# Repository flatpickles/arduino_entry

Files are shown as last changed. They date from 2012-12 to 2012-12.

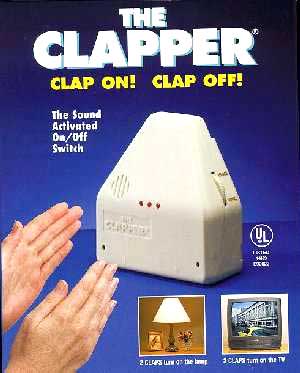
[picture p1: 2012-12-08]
final_paper/the-clapper.jpg

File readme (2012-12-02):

Arduino Entry System
Fall 2012
Andy Chen, Max Lesser, Matt Nichols

OVERVIEW

This project is a reasonably straightforward Arduino program which enables pulling the deadbolt from the inside of a door once a specific pattern of knocks has been detected. This pattern is configurable via a "record" function, and, when powered, the device is always listening for the pattern, ready to trigger a motor to pull the deadlock.

DESIGN

This program assumes a hardware configuration that includes a piezo element for knock sensing (connected on "piezo_pin", in our code), two LEDs for control output, a button to trigger the recording mode, and a servo ("s1", connected on "servo_pin") to pull the deadbolt.

The device begins with a default knock pattern of ten equally spaced knocks. In our system, a n knock pattern is represented as a n-1 sized array, each element being the ratio between adjacent knocks (so the default knock pattern is represented as [1, 1, 1, 1, 1, 1, 1, 1, 1]). When the system hears a first knock, it will begin recording the time offsets between subsequent knocks, and after a timeout (i.e. the knock has completed) relative ratios are calculated from the recorded offsets. Each of these ratios are then compared to those of the current key pattern (within an error margin), and if they all match then the servo is triggered and the deadbolt is pulled open.

Recording is very similar: pressing the button triggers record mode, and then the current key pattern will be replaced by whatever ratioed pattern is recorded after the button press (and before a timeout, as above). This pattern will then be played back to the user on a LED, and the device will re-enter normal operation, listening for entry attempts.

USE

Installation: the device must be installed such that the piezo is pressed directly against the door, to best register knocking. The servo should be configured to pull the deadbolt out when it rotates (the user will need to handle re-locking the door).

Recording: press the button once, and then knock out the desired pattern on the inside of the door. Wait for the timeout, and then make sure the replayed pattern (on the second, lower LED) is as you desire. Your patterns must consist of between three and ten knocks (inclusive); shorter knocks will not overwrite the current key pattern, and recording will cut off after ten knocks.

Unlocking: simply knock the pre-recorded pattern on the outside of the door, and if the time ratios between your knocks match the stored key pattern, the servo will pull the deadlock. It must be manually re-locked afterwards. If you make a mistake in the pattern, wait four seconds (the timeout) and try again.

NEXT STEPS

In the remote_unlock/ directory of the repo, we have the backend/server script for implementing SMS-triggered unlocking as well (via Twilio). Alas, we haven't yet had any successes in configuring the device's side of this functionality; however, should the device be configured with an ethernet shield, it would be simple to poll against [server port]/state and trigger the servo when the "Unlocked" state is observed.

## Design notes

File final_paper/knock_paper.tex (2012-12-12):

%==============================================================================
% Matt Nichols' Homework Template
%==============================================================================

%Fill out this line with the homework number
\newcommand{\visibleusernames}
{\space man1, malesser, ac110 }
{}
\newcommand{\thisclass}{CSCI 160}
\newcommand{\thishw}{Final Project}

%==============================================================================
% Formatting parameters
%==============================================================================

\documentclass[11pt]{article}			% 11pt article
\author{Matt Nichols}
\date{\today}
\makeatletter					% Make '@' accessible.

%Fill out this line with your name and login
\def\@oddhead{\bf \thisclass \space - \thishw\hfill \visibleusernames} % Here they are

\oddsidemargin=0in				% Left margin minus 1 inch.
\evensidemargin=0in				% Same for even-numbered pages.
\textwidth=6.5in				% Text width (8.5in - margins).
\topmargin=0in					% Top margin minus 1 inch.
\headsep=0.2in					% Distance from header to body.
\textheight=8.5in					% Body height (incl. footnotes)
\skip\footins=4ex				% Space above first footnote.
\hbadness=10000					% No "underfull hbox" messages.
\makeatother					% Make '@' special again.

%==============================================================================
% Packages used
%==============================================================================

\usepackage{amsmath}				% want AMS fonts
\usepackage{amssymb}
%\usepackage{psfig}				% want to include EPS files
\usepackage[pdftex]{graphicx}				% for including images
\usepackage{algorithmic}
\usepackage{algorithm}
\usepackage{hyperref}
\usepackage{tikz}

%==============================================================================
% Macros
%==============================================================================
\newcommand{\new}[1]{{\em #1\/}}		% New term (set in italics).
\newcommand{\set}[1]{\{#1\}}			% Set (as in \set{1,2,3})
\newcommand{\setof}[2]{\{\,{#1} $\mid$~{#2}\,\}}	% Set (as in \setof{x}{x > 0})
\newcommand{\N}{\mathord{\Bbb N}}		% Positive integers.
\newcommand{\compl}[1]{\overline{#1}}		% Complement of ...            
\newcommand{\bigand}{\bigwedge}
\newcommand{\bigor}{\bigvee}
\newcommand{\OR}{\vee}
\newcommand{\AND}{\wedge}
\newcommand{\code}[1]{\texttt{#1}}
\newcommand{\nlogn}{n \log n}

\newcounter{qcounter}
\setcounter{section}{0}
\def\thesection{Section \arabic{section}}

% \begin{list}{b\alph{qcounter}.}{\usecounter{qcounter}} <-- helpful

%==============================================================================
% Title
%==============================================================================

\begin{document}
\centerline{\bf \LARGE\thishw: Knock Detection Entry System}
\centerline{\today}

\section{Introduction}
 % Introduce your project. Succinctly explain your problem and solution. Why did you choose to work on it?
Carrying keys around has always been a hassle for all of us. If one loses a key, he or she has to be assisted by someone else to get in to the room. In addition, there are many situations where you wouldn't want to bring your keys with you either, such as when you're going on a run. We wanted an easier way to enter and exit a locked room, and not ever have to worry about being locked out. 

Our project involves an Arduino program which enables pulling a door handle down from the inside of a door once a specific pattern of knocks has been detected. This pattern is configurable via a ``record" function, and, when powered, the device is always listening for the pattern, ready to trigger a motor to open the door. If an incorrect knock pattern is given, the program alerts you through a buzz in the speaker. This way, the room is secure, and you'll never be locked out because you don't have the key.

\section{Architecture}
% Describe the architecture of your system. Figures are welcomed and encouraged

\subsection{Hardware Design}

This program assumes a hardware configuration that includes a piezo element for knock sensing (connected on \verb|piezo_pin|, in our code), two LEDs for control output, a button to trigger the recording mode, a servo (\verb|s1|, connected on \verb|servo_pin|) to pull the deadbolt, and a second piezo speaker to buzz when an incorrect pattern is recognized, or the system times out (and starts waiting for another knock series).

The wiring of the system ended up being pretty straightforward (see diagram below). The piezo on the left is for audio output (signaling error events or a reset of the listening system) and the piezo on the right (highlighted in purple) is used for knock detection. The left (red) LED blinks whenever a knock is detected (mainly a debugging tool for us, though also helpful when the user is recording), and the right (green) LED is a control signal: it is turned on during recording, and is used to both signal a timeout event (reset of input knock pattern) and to replay a knock pattern to the user after it has been recorded. When the system receives a correct knock pattern, it will rotate the servo 180 degrees (enough to pull down a door handle or draw back a deadlock), wait a few seconds, and then rotate back to its original position. The rest of our hardware implementation is reasonably simple, but is diagrammed in full below.

\begin{center}

\end{center}

\subsection{Software Design}

Left to describe is the operation of our software which is running on the Arduino, which is strictly procedural and adheres to a predetermined flow (i.e. we do not make use of interrupts on the Arduino platform).

The basic operation of our software can be summed up well as a finite state machine (below). The system's default state is iterating within the Arduino main loop, waiting for either a button press or a knock. At both \verb|Input| and \verb|Record|, it will continue listening for subsequent knocks, though the transitions out of these states are different: at \verb|Input|, it will only move on to evaluation of the knock pattern once \verb|n knocks| (the number of knocks in the current valid pattern) have been detected, while at \verb|Record|, it will wait for a timeout (i.e. knocking has stopped) or until the user has input the maximum allowable number of knocks to progress to the next state. Along both the \verb|timeout| and \verb|incorrect| edges, a sound will be played on the speaker. The \verb|Print| state corresponds to a blocking process during which the current valid pattern is echoed in appropriately spaced blinks on the control LED, and after this completes, it returns to its normal resting state. The rest of the system's operation within the state diagram should be self-explanatory, though we delve into a few more details (outside of the FSM) below.

\begin{center}
\begin{tikzpicture}[scale=0.2]
\tikzstyle{every node}+=[inner sep=0pt]
\draw [black] (26.6,-22.6) circle (3);
\draw (26.6,-22.6) node {$Loop$};
\draw [black] (55,-41.3) circle (3);
\draw (55,-41.3) node {$Input$};
\draw [black] (67.6,-23.2) circle (3);
\draw (67.6,-23.2) node {$Record$};
\draw [black] (26.6,-51.2) circle (3);
\draw (26.6,-51.2) node {$Check$};
\draw [black] (6,-51.2) circle (3);
\draw (6,-51.2) node {$Open$};
\draw [black] (6,-51.2) circle (2.4);
\draw [black] (26.6,-7.6) circle (3);
\draw (26.6,-7.6) node {$Print$};
\draw [black] (29.6,-22.64) -- (64.6,-23.16);
\fill [black] (64.6,-23.16) -- (63.81,-22.64) -- (63.79,-23.64);
\draw (47.08,-23.48) node [below] {$button\mbox{ }press$};
\draw [black] (29.11,-24.25) -- (52.49,-39.65);
\fill [black] (52.49,-39.65) -- (52.1,-38.79) -- (51.55,-39.63);
\draw (37.85,-32.45) node [below] {$knock$};
\draw [black] (23.713,-23.373) arc (312.7283:24.7283:2.25);
\draw (19.24,-20.97) node [left] {$no\mbox{ }input$};
\fill [black] (24.23,-20.78) -- (24.05,-19.85) -- (23.32,-20.53);
\draw [black] (52.49,-39.65) -- (29.11,-24.25);
\fill [black] (29.11,-24.25) -- (29.5,-25.11) -- (30.05,-24.27);
\draw (44.45,-31.45) node [above] {$timeout$};
\draw [black] (52.17,-42.29) -- (29.43,-50.21);
\fill [black] (29.43,-50.21) -- (30.35,-50.42) -- (30.02,-49.48);
\draw (37.07,-45.62) node [above] {$n\mbox{ }knocks$};
\draw [black] (23.6,-51.2) -- (9,-51.2);
\fill [black] (9,-51.2) -- (9.8,-51.7) -- (9.8,-50.7);
\draw (16.3,-50.7) node [above] {$correct$};
\draw [black] (57.982,-41.109) arc (121.40093:-166.59907:2.25);
\draw (61.97,-44.82) node [right] {$knock$};
\fill [black] (56.97,-43.55) -- (56.96,-44.49) -- (57.81,-43.97);
\draw [black] (26.6,-48.2) -- (26.6,-25.6);
\fill [black] (26.6,-25.6) -- (26.1,-26.4) -- (27.1,-26.4);
\draw (27.1,-36.9) node [right] {$incorrect$};
\draw [black] (7.75,-48.77) -- (24.85,-25.03);
\fill [black] (24.85,-25.03) -- (23.97,-25.39) -- (24.78,-25.98);
\draw (16.89,-38.28) node [right] {$timeout$};
\draw [black] (64.8,-22.13) -- (29.4,-8.67);
\fill [black] (29.4,-8.67) -- (29.97,-9.42) -- (30.33,-8.48);
\draw (55.86,-14.69) node [above] {$timeout\mbox{ }/\mbox{ }max\mbox{ }knocks$};
\draw [black] (26.6,-10.6) -- (26.6,-19.6);
\fill [black] (26.6,-19.6) -- (27.1,-18.8) -- (26.1,-18.8);
\draw (26.1,-15.1) node [left] {$done\mbox{ }printing$};
\draw [black] (69.27,-20.722) arc (173.74488:-114.25512:2.25);
\draw (74.12,-18.63) node [right] {$knock$};
\fill [black] (70.58,-23.02) -- (71.32,-23.6) -- (71.43,-22.61);
\draw [black] (56.71,-38.84) -- (65.89,-25.66);
\fill [black] (65.89,-25.66) -- (65.02,-26.03) -- (65.84,-26.6);
\draw (61.9,-33.61) node [right] {$button\mbox{ }press$};
\end{tikzpicture}
\end{center}

The device begins with a default knock pattern of ten equally spaced knocks. In our system, an $n$ knock pattern is represented as a $n-1$ sized array, each element being the ratio between adjacent knocks (so the default knock pattern is represented as $[1, 1, 1, 1, 1, 1, 1, 1, 1]$). When the system hears a first knock, it will begin recording the time offsets between subsequent knocks, and after it receives the number of expected knocks, relative ratios are calculated from the recorded offsets. Each of these ratios are then compared to those of the current key pattern (within an error margin), and if they all match then the servo is triggered and the deadbolt is pulled open.

Recording is very similar: pressing the button triggers record mode, and then the current key pattern will be replaced by whatever ratioed pattern is recorded after the button press (and before a timeout, as stated). This pattern will then be played back to the user on a LED (as mentioned above), and the device will re-enter normal operation, listening for entry attempts. If fewer than three knocks are recorded during this process, the valid key pattern will not be replaced, and the previously (and still) valid key pattern will be what is played back on the LED.

\subsection{Conceptual}

Following is a basic overview for how we imagine an end user approaching the operation of our device. After the above explanation, these things may be evident, but consider this the higher-level, more conceptual, usability-oriented side of our design. 

\textbf{Installation:} the device must be installed such that the piezo is pressed directly against the door, to best register vibrations caused by knocking. The servo should be configured to pull the deadbolt or door handle when it rotates.

\textbf{Recording:} press the button once, and then knock out the desired pattern on the inside of the door. Wait for the timeout, and then make sure the replayed pattern (on the second, lower LED) is as you desire. Your patterns must consist of between three and ten knocks (inclusive); shorter knock patterns will not overwrite the current key pattern, and recording will cut off after ten knocks.

\textbf{Unlocking:} simply knock the pre-recorded pattern on the outside of the door, and if the time ratios between your knocks match the stored key pattern, the servo will pull the deadlock or door handle. It must be manually re-locked afterwards. If you make a mistake in the pattern, wait four seconds (the timeout) and try again.

\section{Implementation}
% Challenges, etc.

In this section, we will briefly discuss some specific design choices we made in our implementation.

\textbf{Timeout}: We chose a timeout of 4 seconds. From a user standpoint, we decided it was the right amount of time because 4 seconds between knocks is too long for a pattern, and isn't so long that the user would get impatient waiting for it to timeout.

\textbf{Threshold}: We have a threshold of 0.5. This means that the most any interval between knocks can be wrong by is 0.5. For example, if the interval between 2 knocks is 3, a ``correct" input is anywhere from 2.5 to 3.5. After multiple trials we discovered that this constant was the perfect error margin for a standard user.

\textbf{Knock threshold}: This threshold sets how loud a knock has to be in order to be registered. We chose 3 because it detects most knocks, and no static.

\textbf{Keeping door open}: The door stays open for 3 seconds, and nothing can happen with the program for 2 seconds after it closes. The door stays open that long because it's the right amount of time to give the user to enter. We had to block the program for 2 seconds after it closes becasue it would mess up the circuit voltages.

\textbf{Max number of knocks}: We limited the user to a maximum number of 10 knocks for their pattern. We chose this number because it allows for creativity and unique knocking patterns. We limited it to 10 because longer knock patterns would result in the user forgetting the pattern.

\textbf{Debounce-delay}: The sensor doesn't detect a knock as a singular event. It will detect a singular knock as many knocks that happen 
extremely close together. We need a debounce delay to make the program wait to make sure the program doesnt think the vibrations after the knock are more knocks. We chose .1 seconds because you would never try to do two knocks that quickly, and it fixes the problem stated.

\section{Evaluation}
% did it work? Are there any corner cases? How would you solve them?
We were able to successfully connect the finished product to a door.  The piezo sensor used to detect knocks is fairly cheap, so sometimes knocks are not detected correctly, but it works fairly well.  To get the best results, the components must be placed somewhere in the center of the door so that all vibrations are picked up clearly.  

Recording and playback of patterns works perfectly, and with the addition of a piezo speaker it is easy to tell when you haven't correctly knocked out the pattern, or your knocks have timed out.  One problem with the finished product is that the servo we purchased only is able to turn 180 degrees.  This means that it is only able to pull a doorknob or lock a small distance.  We were able to solve this problem by pre-pulling the knob a small amount, so that the knob only has to be pulled a small amount before the door is opened.

One edge case to deal with is ambient vibrations in the door that the system is connected to.  If it picks up stray vibrations, it could either mess up the pattern the user is trying to knock out, or pick up knocks when the user isn't even using the device.  Luckily, the first problem is solved by merely re-knocking the pattern, as the buzzer lets you know when you have made a mistake.  If knocks are being picked up when the user isn't knocking at all, the buzzer will sound after a timeout, but nothing else will happen.

\section{Related Work}
% Are there any similar solutions? Compare yours to theirs, if possible.
There aren't many similar affordable solutions. Doorknob setups with fingerprint scanners exist but are extremely expensive, costing around \$300.

``The Clapper" also exists, that gives current to an outlet if it detects claps, and this could potentially be used to implement a similar door-opening system. However, it doesn't let you customize the sequence of claps. It doesn't directly connect to a motor either. Lastly, it detects sound as opposed to vibrations. Our project won't detect random noises, only vibrations on the door whereas ``The Clapper" could interpret white noise and randomly open and close the door. ``The Clapper" goes for around \$20. 

Probably the best alternative to our solution is Lockitron: a Kickstarter project that uses smart phones to lock and unlock doors. To use Lockitron, you first need to attach the Lockitron shell around your deadbolt. This shell is smart; it's connected to WiFi and has Bluetooth. From anywhere in the world, you can unlock or lock your door from your smartphone. You can also grant access to other users. Lockitron also automatically unlocks the door when you walk near it with your smartphone. With Lockitron, you would still either need your key or a phone to get into you're locked house. It doesn't entirely address the problem we were having. You can still lock your phone inside the house, and if you don't want to run with keys, why would you run with your phone. We need a solution that doesn't physically require any hardware, and Lockitron doesn't give us that. It also costs around \$200. The device can be pre-ordered at: \url{www.lockitron.com/preorder}

Our project's cost came out to around \$50. If we were to sell this project, our costs would decrease due to ordering parts in bulk, so we could sell for around \$70 and turn a fairly significant profit.

\section{Future Work}
% Describe here features that you wanted to implement, but due to time/resource constraints you weren't able to.

If we had had the time, our first stretch goal for this project was to implement remote unlocking via SMS messaging. The basic idea here would be to send a text to a specific number with a control command (eg. ``open'' or ``close''), and if this message originates from a verified number the command would be executed on the device. This could work well as both an override (if we forget the pattern), as well as a good way to let friends into a room which you're not in, et cetera.

We managed to write the backend (i.e. server code) for this aspect of the application, though didn't have time to implement the hardware and Arduino code side of this system. In the \verb|remote_unlock/| directory of our repo and project handin, we have a script which runs as a Twilio endpoint (see \url{www.twilio.com}), and also has a route to advertise the current (intended) state of the device. Assuming we had our board hooked up to an ethernet connection from which we could access the server, it would be simple to poll against \verb|[server port]/state| and trigger the servo when the ``Unlocked" state is observed.

Two further improvements which could be made to our device are making it battery powered (currently it must be connected to a laptop or a wall socket at all times) and having audio as well as visual playback for echoing recorded patterns.

\end{document}

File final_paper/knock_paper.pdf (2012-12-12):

CSCI 160 - Final Project | man1, malesser, ac110

## Final Project: Knock Detection Entry System

December 11, 2012

## Section 1 Introduction

Carrying keys around has always been a hassle for all of us. If one loses a key, he or she has to be assisted by someone else to get in to the room. In addition, there are many situations where you wouldn’t want to bring your keys with you either, such as when you’re going on a run. We wanted an easier way to enter and exit a locked room, and not ever have to worry about being locked out. Our project involves an Arduino program which enables pulling a door handle down from the inside of a door once a specific pattern of knocks has been detected. This pattern is configurable via a “record” function, and, when powered, the device is always listening for the pattern, ready to trigger a motor to open the door. If an incorrect knock pattern is given, the program alerts you through a buzz in the speaker. This way, the room is secure, and you’ll never be locked out because you don’t have the key.

Section 2 | Architecture
Section 2.1 | Hardware Design

This program assumes a hardware configuration that includes a piezo element for knock sensing (connected on piezo_pin, in our code), two LEDs for control output, a button to trigger the recording mode, a servo (s1, connected on servo_pin) to pull the deadbolt, and a second piezo speaker to buzz when an incorrect pattern is recognized, or the system times out (and starts waiting for another knock series).
The wiring of the system ended up being pretty straightforward (see diagram below). The piezo on the left is for audio output (signaling error events or a reset of the listening system) and the piezo on the right (highlighted in purple) is used for knock detection. The left (red) LED blinks whenever a knock is detected (mainly a debugging tool for us, though also helpful when the user is recording), and the right (green) LED is a control signal: it is turned on during recording, and is used to both signal a timeout event (reset of input knock pattern) and to replay a knock pattern to the user after it has been recorded. When the system receives a correct knock pattern, it will rotate the servo 180 degrees (enough to pull down a door handle or draw back a deadlock), wait a few seconds, and then rotate back to its original position. The rest of our hardware implementation is reasonably simple, but is diagrammed in full below.

CSCI 160 - Final Project | man1, malesser, ac110

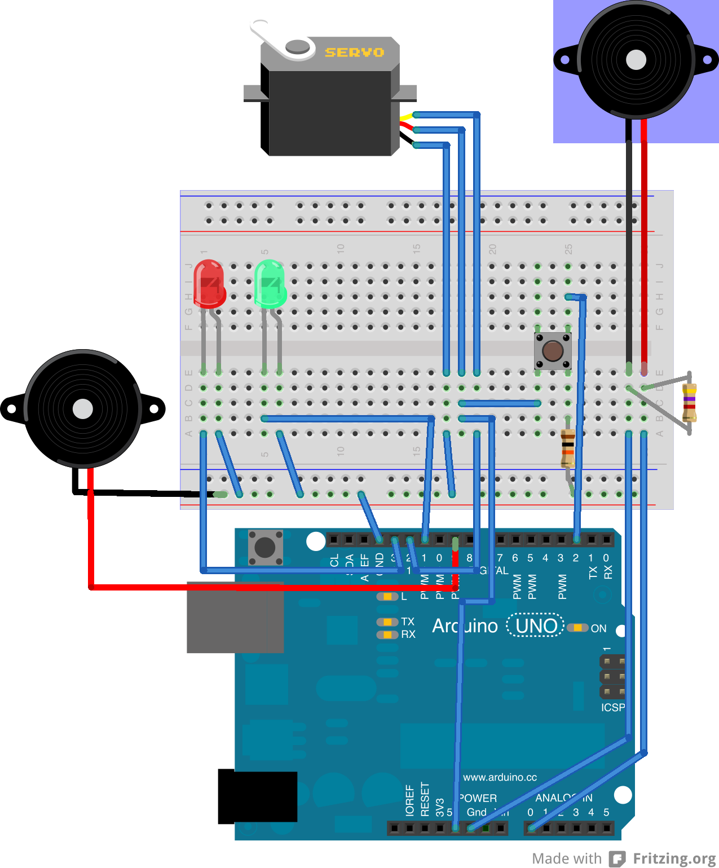
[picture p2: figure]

Section 2.2 | Software Design

Left to describe is the operation of our software which is running on the Arduino, which is strictly procedural and adheres to a predetermined flow (i.e. we do not make use of interrupts on the Arduino platform).
The basic operation of our software can be summed up well as a finite state machine (below). The system’s default state is iterating within the Arduino main loop, waiting for either a button press or a knock. At both Input and Record, it will continue listening for subsequent knocks, though the transitions out of these states are different: at Input, it will only move on to evaluation of the knock pattern once n knocks (the number of knocks in the current valid pattern) have been detected, while at Record, it will wait for a timeout (i.e. knocking has stopped) or until the user has input the maximum allowable number of knocks to progress to the next state. Along both the timeout and incorrect edges, a sound will be played on the speaker. The Print state corresponds to a blocking process during which the current valid pattern is echoed in appropriately spaced blinks

CSCI 160 - Final Project | man1, malesser, ac110

on the control LED, and after this completes, it returns to its normal resting state. The rest of the system’s operation within the state diagram should be self-explanatory, though we delve into a few more details (outside of the FSM) below.

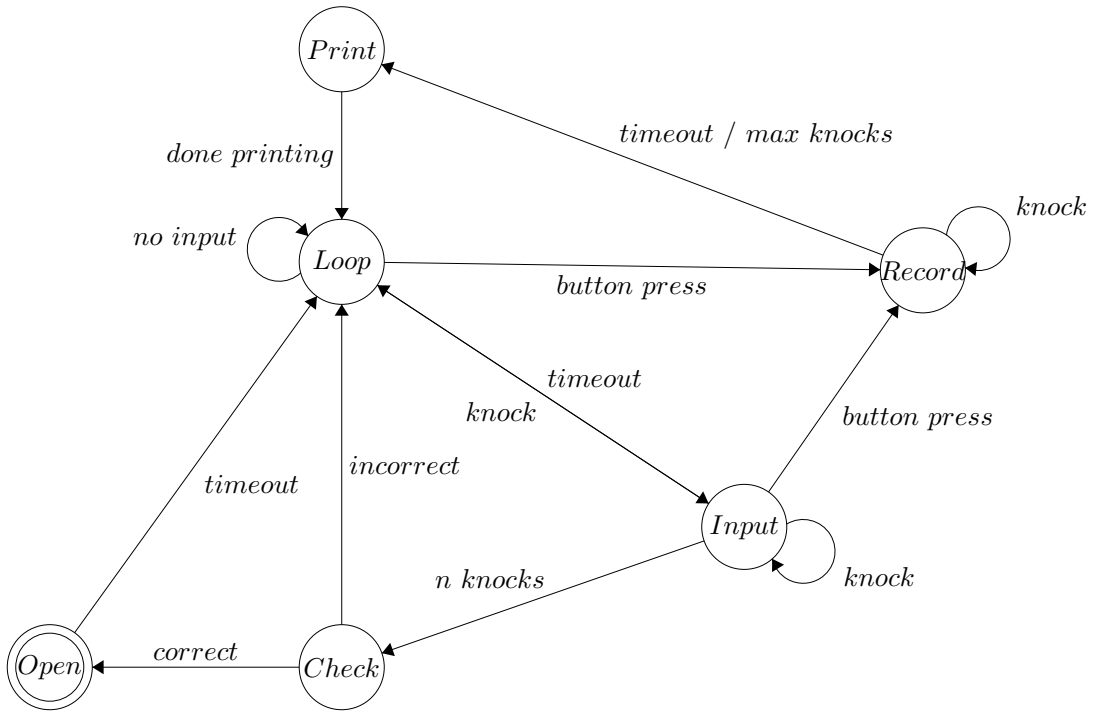
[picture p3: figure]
Loop; Input; Record; Open; Check; P rint; button press; knock; no input; timeout; n knocks; correct; incorrect; timeout / max knocks; done printing

The device begins with a default knock pattern of ten equally spaced knocks. In our system, an n knock pattern is represented as a n − 1 sized array, each element being the ratio between adjacent knocks (so the default knock pattern is represented as [1, 1, 1, 1, 1, 1, 1, 1, 1]). When the system hears a first knock, it will begin recording the time offsets between subsequent knocks, and after it receives the number of expected knocks, relative ratios are calculated from the recorded offsets. Each of these ratios are then compared to those of the current key pattern (within an error margin), and if they all match then the servo is triggered and the deadbolt is pulled open. Recording is very similar: pressing the button triggers record mode, and then the current key pattern will be replaced by whatever ratioed pattern is recorded after the button press (and before a timeout, as stated). This pattern will then be played back to the user on a LED (as mentioned above), and the device will re-enter normal operation, listening for entry attempts. If fewer than three knocks are recorded during this process, the valid key pattern will not be replaced, and the previously (and still) valid key pattern will be what is played back on the LED.

Section 2.3 Conceptual

Following is a basic overview for how we imagine an end user approaching the operation of our device. After the above explanation, these things may be evident, but consider this the higher-level, more conceptual, usability-oriented side of our design.

CSCI 160 - Final Project | man1, malesser, ac110

Installation: the device must be installed such that the piezo is pressed directly against the door, to best register vibrations caused by knocking. The servo should be configured to pull the deadbolt or door handle when it rotates.
Recording: press the button once, and then knock out the desired pattern on the inside of the door. Wait for the timeout, and then make sure the replayed pattern (on the second, lower LED) is as you desire. Your patterns must consist of between three and ten knocks (inclusive); shorter knock patterns will not overwrite the current key pattern, and recording will cut off after ten knocks.
Unlocking: simply knock the pre-recorded pattern on the outside of the door, and if the time ratios between your knocks match the stored key pattern, the servo will pull the deadlock or door handle. It must be manually re-locked afterwards. If you make a mistake in the pattern, wait four seconds (the timeout) and try again.

## Section 3 Implementation

In this section, we will briefly discuss some specific design choices we made in our implementation. Timeout: We chose a timeout of 4 seconds. From a user standpoint, we decided it was the right amount of time because 4 seconds between knocks is too long for a pattern, and isn’t so long that the user would get impatient waiting for it to timeout.
Threshold: We have a threshold of 0.5. This means that the most any interval between knocks can be wrong by is 0.5. For example, if the interval between 2 knocks is 3, a “correct” input is anywhere from 2.5 to 3.5. After multiple trials we discovered that this constant was the perfect error margin for a standard user.
Knock threshold: This threshold sets how loud a knock has to be in order to be registered. We chose 3 because it detects most knocks, and no static.
Keeping door open: The door stays open for 3 seconds, and nothing can happen with the program for 2 seconds after it closes. The door stays open that long because it’s the right amount of time to give the user to enter. We had to block the program for 2 seconds after it closes becasue it would mess up the circuit voltages.
Max number of knocks: We limited the user to a maximum number of 10 knocks for their pattern. We chose this number because it allows for creativity and unique knocking patterns. We limited it to 10 because longer knock patterns would result in the user forgetting the pattern. Debounce-delay: The sensor doesn’t detect a knock as a singular event. It will detect a singular knock as many knocks that happen extremely close together. We need a debounce delay to make the program wait to make sure the program doesnt think the vibrations after the knock are more knocks. We chose .1 seconds because you would never try to do two knocks that quickly, and it fixes the problem stated.

## Section 4 Evaluation

We were able to successfully connect the finished product to a door. The piezo sensor used to detect knocks is fairly cheap, so sometimes knocks are not detected correctly, but it works fairly well. To get the best results, the components must be placed somewhere in the center of the door so that all vibrations are picked up clearly.

CSCI 160 - Final Project | man1, malesser, ac110

Recording and playback of patterns works perfectly, and with the addition of a piezo speaker it is easy to tell when you haven’t correctly knocked out the pattern, or your knocks have timed out. One problem with the finished product is that the servo we purchased only is able to turn 180 degrees. This means that it is only able to pull a doorknob or lock a small distance. We were able to solve this problem by pre-pulling the knob a small amount, so that the knob only has to be pulled a small amount before the door is opened.
One edge case to deal with is ambient vibrations in the door that the system is connected to. If it picks up stray vibrations, it could either mess up the pattern the user is trying to knock out, or pick up knocks when the user isn’t even using the device. Luckily, the first problem is solved by merely re-knocking the pattern, as the buzzer lets you know when you have made a mistake. If knocks are being picked up when the user isn’t knocking at all, the buzzer will sound after a timeout, but nothing else will happen.

## Section 5 Related Work

There aren’t many similar affordable solutions. Doorknob setups with fingerprint scanners exist but are extremely expensive, costing around $300.
“The Clapper” also exists, that gives current to an outlet if it detects claps, and this could potentially be used to implement a similar door-opening system. However, it doesn’t let you customize the sequence of claps. It doesn’t directly connect to a motor either. Lastly, it detects sound as opposed to vibrations. Our project won’t detect random noises, only vibrations on the door whereas “The Clapper” could interpret white noise and randomly open and close the door. “The Clapper” goes for around $20.
Probably the best alternative to our solution is Lockitron: a Kickstarter project that uses smart phones to lock and unlock doors. To use Lockitron, you first need to attach the Lockitron shell around your deadbolt. This shell is smart; it’s connected to WiFi and has Bluetooth. From anywhere in the world, you can unlock or lock your door from your smartphone. You can also grant access to other users. Lockitron also automatically unlocks the door when you walk near it with your smartphone. With Lockitron, you would still either need your key or a phone to get into you’re locked house. It doesn’t entirely address the problem we were having. You can still lock your phone inside the house, and if you don’t want to run with keys, why would you run with your phone. We need a solution that doesn’t physically require any hardware, and Lockitron doesn’t give us that. It also costs around $200. The device can be pre-ordered at: www.lockitron.com/preorder Our project’s cost came out to around $50. If we were to sell this project, our costs would decrease due to ordering parts in bulk, so we could sell for around $70 and turn a fairly significant profit.

## Section 6 Future Work

If we had had the time, our first stretch goal for this project was to implement remote unlocking via SMS messaging. The basic idea here would be to send a text to a specific number with a control command (eg. “open” or “close”), and if this message originates from a verified number the command would be executed on the device. This could work well as both an override (if we forget the pattern), as well as a good way to let friends into a room which you’re not in, et cetera.

CSCI 160 - Final Project | man1, malesser, ac110

We managed to write the backend (i.e. server code) for this aspect of the application, though didn’t have time to implement the hardware and Arduino code side of this system. In the remote_unlock/ directory of our repo and project handin, we have a script which runs as a Twilio endpoint (see www.twilio.com), and also has a route to advertise the current (intended) state of the device. Assuming we had our board hooked up to an ethernet connection from which we could access the server, it would be simple to poll against [server port]/state and trigger the servo when the “Unlocked” state is observed.
Two further improvements which could be made to our device are making it battery powered (currently it must be connected to a laptop or a wall socket at all times) and having audio as well as visual playback for echoing recorded patterns.

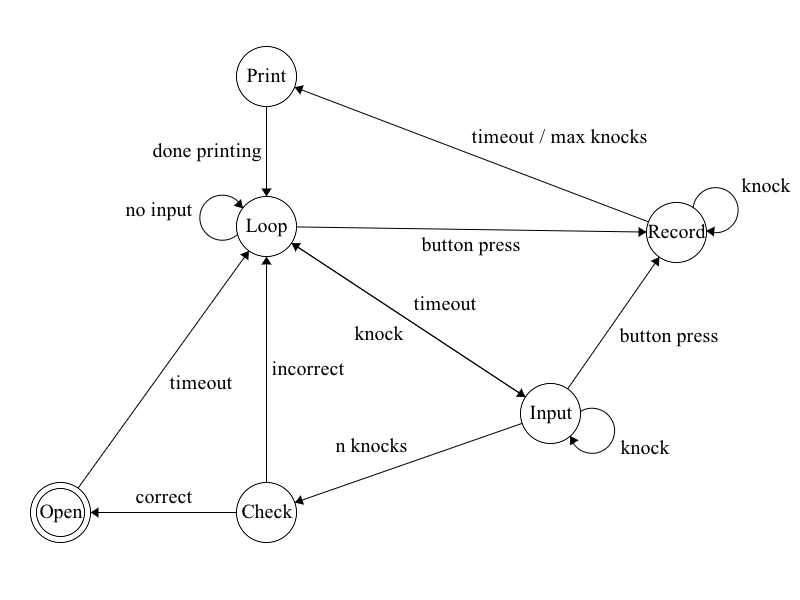
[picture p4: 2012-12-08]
final_paper/fsm.png

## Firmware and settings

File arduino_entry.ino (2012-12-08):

#include <Servo.h>

#define TIMEOUT 4000
#define THRESHOLD .5

// globals to manage knock sensing
int piezo_pin = 0;
int led_pin = 13;
int servo_pin = 12;
int knock_threshold = 3;
int led_pin_2 = 11;
int button_pin = 2;
long debounce_delay = 100;
long last;

// speaker
int speakerOut = 9;

// globals to manage opening and open state
Servo s1;
int closed_val = 0;
int open_val = 180;
int open_state = 0;
long opened_at = 0; // when last opened
long open_for = 3000; // open for 5 seconds
long closed_at = 0; // when last closed
long close_delay = 2000; // wait 2 seconds after closing
long replay_offset = 0;

// pattern detection vars
double to_match[9] = {1, 1, 1, 1, 1, 1, 1, 1, 1};
double temp[9];
double input[9];
unsigned int curr_knock;
long pattern_last = -1;
int total_knocks = 9;
int old_total_knocks = 9;

boolean recording = false;
long last_record;

// configure the device and servo
void setup() {
  Serial.begin(9600);
  pinMode(led_pin, OUTPUT);
  s1.attach(servo_pin);
  s1.write(closed_val);
  pinMode(led_pin_2, OUTPUT);
  pinMode(button_pin, INPUT);
  pinMode(speakerOut, OUTPUT);
}
// loop to poll for knocks and handle related activity
void loop () {

  if (digitalRead(button_pin) == HIGH) {
    recording = true;
    total_knocks = 0;
    curr_knock = 0;
    pattern_last = -1;
    last_record = millis();
    digitalWrite(led_pin_2, HIGH);
  }

  // get current piezo value
  byte val = analogRead(piezo_pin);

  // check for timeout within pattern detectioln
  int cur_time = millis() - pattern_last;
  if (!recording && pattern_last != -1 && cur_time > TIMEOUT) {
    
    curr_knock = 0;
    pattern_last = -1;
    error_tone();
  }

  // finished recording
  if (recording && (millis() - last_record > TIMEOUT || total_knocks == 9)) {
    if(total_knocks > 1)
    {
      for(int x = 0; x < total_knocks; x++)
      {
        to_match[x] = temp[x];
      }
    
      ratio_input_array(to_match, total_knocks);
      old_total_knocks = total_knocks;
    }
    else
      total_knocks = old_total_knocks;
    
    recording = false;
    curr_knock = 0;
      
    // wait and turn off the recording light & last knock light
    delay(debounce_delay * 3);
    digitalWrite(led_pin_2, LOW);
    digitalWrite(led_pin, LOW);
    // replay
    delay(500);
    display_pattern(to_match, total_knocks);
    // debounce
    last = millis();
    
    pattern_last = -1;
  }

  // handle a detected knock
  if (!open_state && closed_at + close_delay < millis() && // if it's not open or recently closed
      val >= knock_threshold && last + debounce_delay < millis()) { // and if value is beyond threshold and we're outside debounce
    // power LED
    digitalWrite(led_pin, HIGH);
    // register in pattern detection
    
    if (pattern_last >= 0) {
      int diff = millis() - pattern_last;
      if (recording == false)
        input[curr_knock] = diff;
      if (recording == true)
      {
        temp[curr_knock] = diff;
        total_knocks++;
      }
      
      curr_knock++;
    }
    // set debounce and pattern timing values
    last = millis();
    pattern_last = millis();
    // if recording
    last_record = millis();
  }

  // handle completed pattern
  if (curr_knock == total_knocks && !recording) {
    // get ratios
    ratio_input_array(input, total_knocks);
    if (compare_array(to_match, input, total_knocks)) 
      open_door();
    else
    {
      error_tone();
    }

    // update to blank slate
    pattern_last = -1;
    curr_knock = 0;
  }
  

  // if it's been open more than open_for millis, close
  if (open_state && opened_at + open_for < millis()) {
    close_door();
  }

  // if no knock sensed and beyond last by 3*debounce, turn led off
  if (last + debounce_delay * 3 < millis()) {
    digitalWrite(led_pin, LOW);
  }
}

/****** Helpers for pattern recognition ******/

// find minimum value within array of length len
double find_min(double array[], int len) {
  int i = 0;
  double cur_min = TIMEOUT;
  for (i = 0; i < len; i++) {
    if(array[i]<cur_min) {
      cur_min = array[i];
    }
  }
  return cur_min;
}

// in place, modify array such that each element is its ratio to the minimum
void ratio_input_array(double array[], int length) {
  double array_min = find_min(array, length);

  int i = 0;
  for (i = 0; i < length; i++) {
    array[i] = array[i] / array_min;
  }
}

// compare timing values in two arrays, within error range
bool compare_array(double match_array[], double input_array[], int length) {
  int i = 0;
  for (int i = 0; i < length; i++) {
    double lower = match_array[i] - THRESHOLD;
    double higher = match_array[i] + THRESHOLD;
    if (input_array[i] > higher || input_array[i] < lower) {
        return false;
    }
  }
  return true;
}

/****** Helpers for lock manipulation ******/

// helper to set open state(s) and write open value to the servo
void open_door() {
  open_state = 1;
  opened_at = millis();
  s1.write(open_val);
}

// helper to set close state(s) and write close value to the servo
void close_door() {
  open_state = 0;
  closed_at = millis();
  s1.write(closed_val);
}

/**** Recording helpers ****/

void display_pattern(double pattern_array[], int length) {
  int base_millis = 300;
  for (int i = 0; i < length; i++) {
    digitalWrite(led_pin_2, HIGH);
    delay(base_millis);
    digitalWrite(led_pin_2, LOW);
    delay(pattern_array[i] * base_millis);
  }
  digitalWrite(led_pin_2, HIGH);
  delay(base_millis);
  digitalWrite(led_pin_2, LOW);
}


// plays a tone when the pattern was not recognized or there was a timeout
void error_tone() {
  long elapsed_time = 0;
  long duration = 300;
  
    while (elapsed_time < duration) {

      digitalWrite(speakerOut,HIGH);
      delayMicroseconds(1912 / 2);

      digitalWrite(speakerOut, LOW);
      delayMicroseconds(1912 / 2);

      elapsed_time += 1;
  }                                 
}

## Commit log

2012-10-28 flashes LED when a knock is detected. Moves motor a little: works
2012-10-31 comments and servo-opening code (after one knock, for now)
2012-10-31 working prototype
2012-12-02 now replays knock pattern on LED after record
2012-12-08 with diagram wooo
    [knock_diagram.fzz]
2012-12-08 state diagram, updating image
    [knock_diagram.fzz]
2012-12-08 fixed knock/record error
    no longer pulls 1 knock before recording
    [arduino_entry.ino]
2012-12-08 adding a bunch of stuff for archetecture
    [knock_diagram.fzz]
